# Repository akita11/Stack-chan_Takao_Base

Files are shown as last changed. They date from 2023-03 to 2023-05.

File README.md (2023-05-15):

# Stack-chan_Takao_Base

現時点で ｽﾀｯｸﾁｬﾝ を組み立てる最もシンプルな方法と思われる、[タカオさん](https://twitter.com/mongonta555)の[タカオ版（旧称：GoBottom版）](https://mongonta.booth.pm/)のための、M5Stack本体と2個のサーボモータ、給電用のUSB TypeCコネクタがついたボードです。電源スイッチもついています。まるごと一式、タカオ版のサーボ固定部分(Bracket)に収納できます。市販のUSB Type-CコネクタつきのACアダプタ等をつないで給電して使用します。以下のように、本体の後ろ側からUSB Type-Cケーブルで給電して動作させることができます。

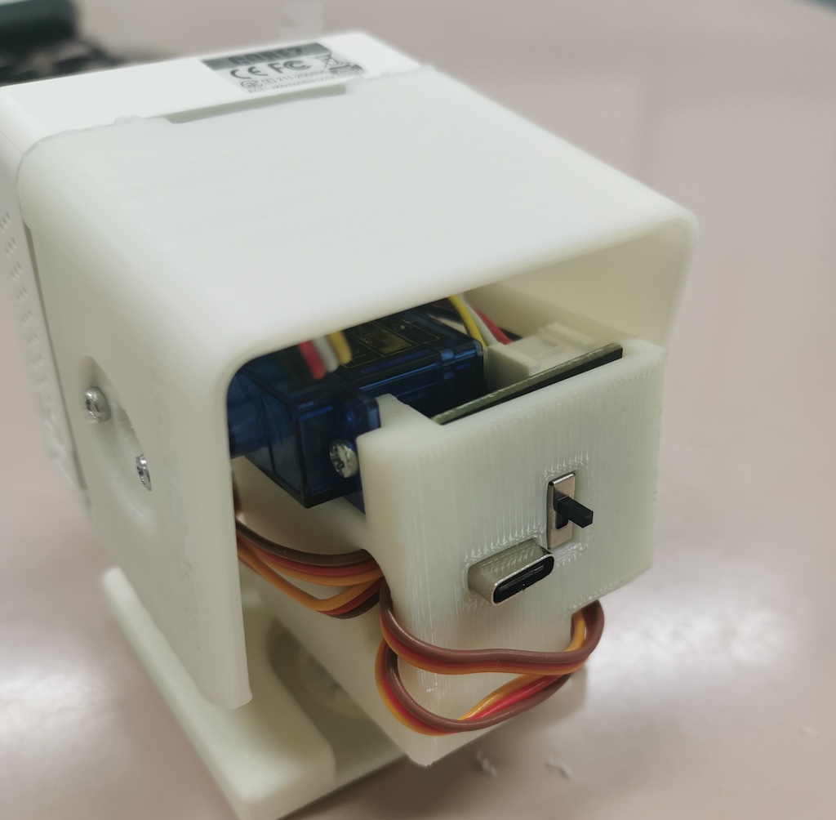
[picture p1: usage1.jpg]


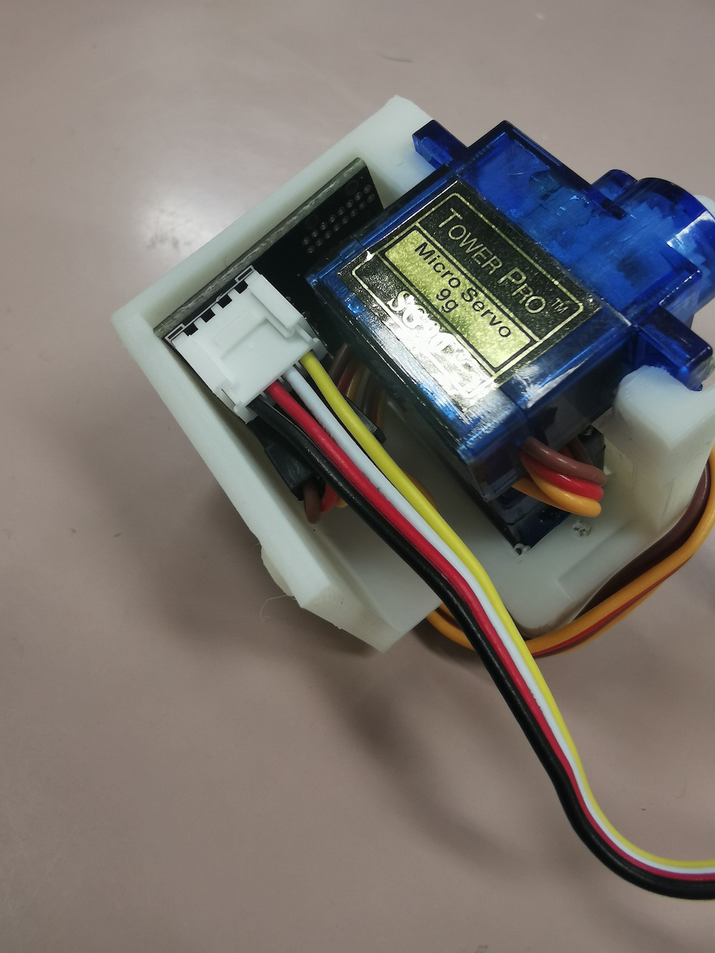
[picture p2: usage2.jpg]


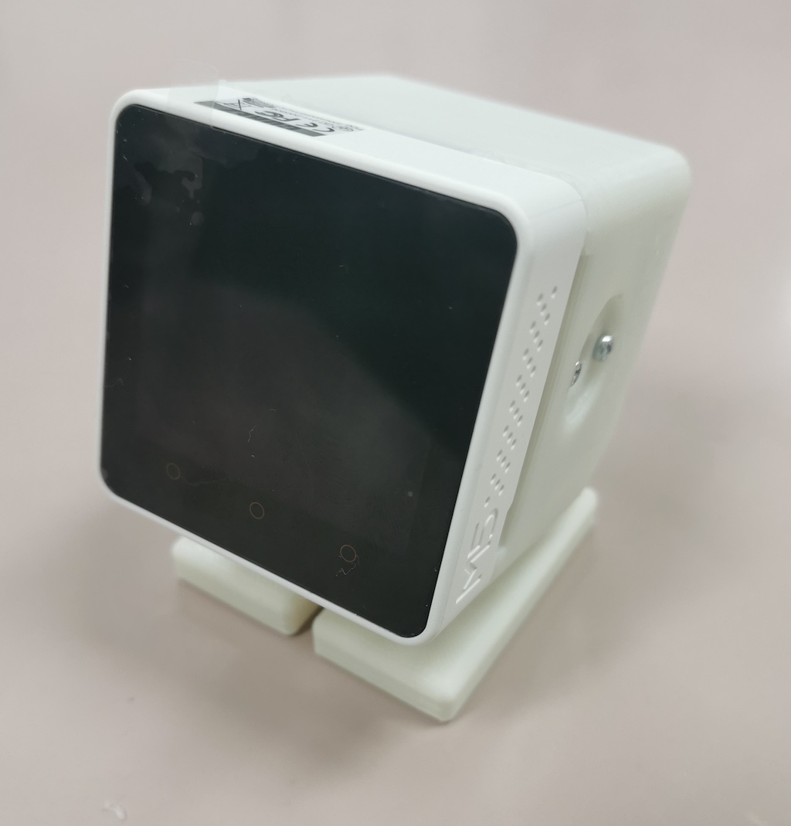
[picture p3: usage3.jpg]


## 表面実装部品版

※[完成品としてスイッチサイエンスで委託販売中](https://www.switch-science.com/products/8905)です

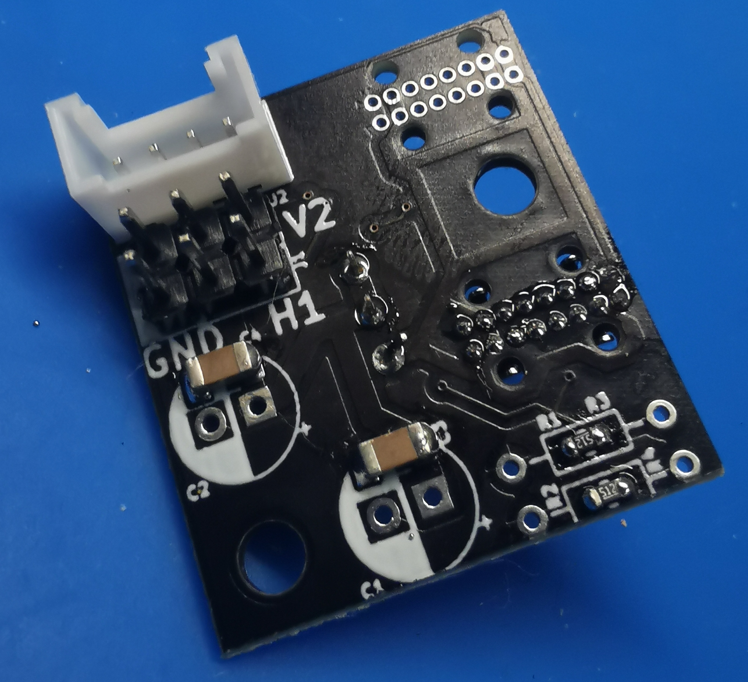
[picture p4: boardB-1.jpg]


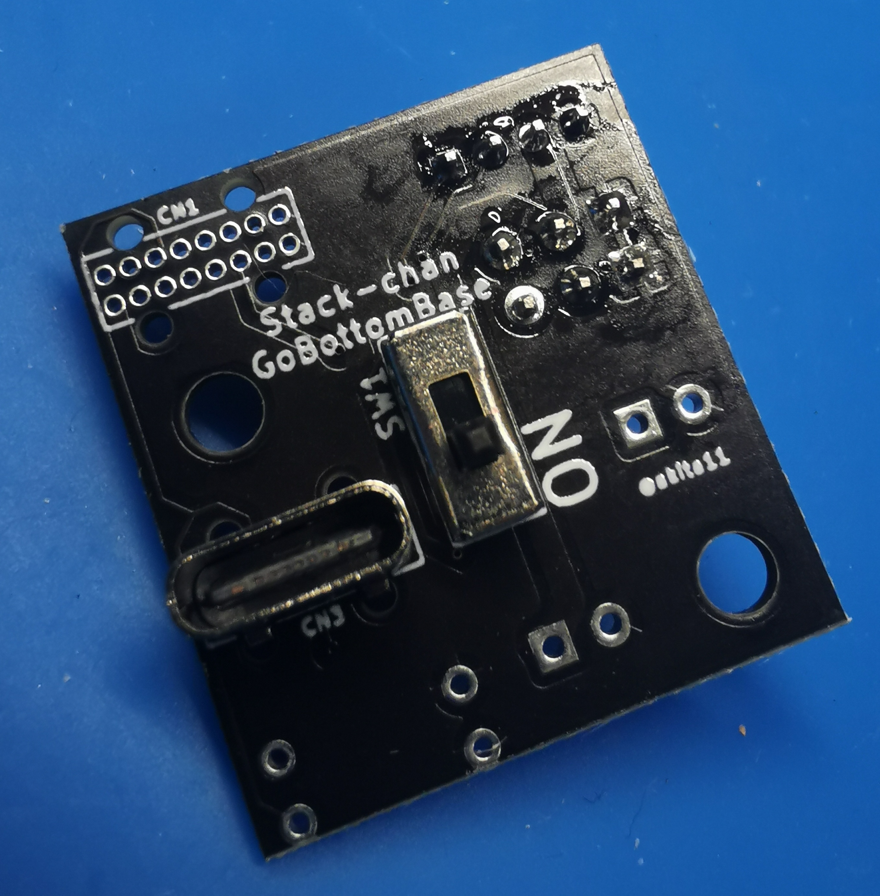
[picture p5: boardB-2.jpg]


## 挿入実装部品版

※[部品キットとしてスイッチサイエンスで委託販売中](https://www.switch-science.com/products/8906)です

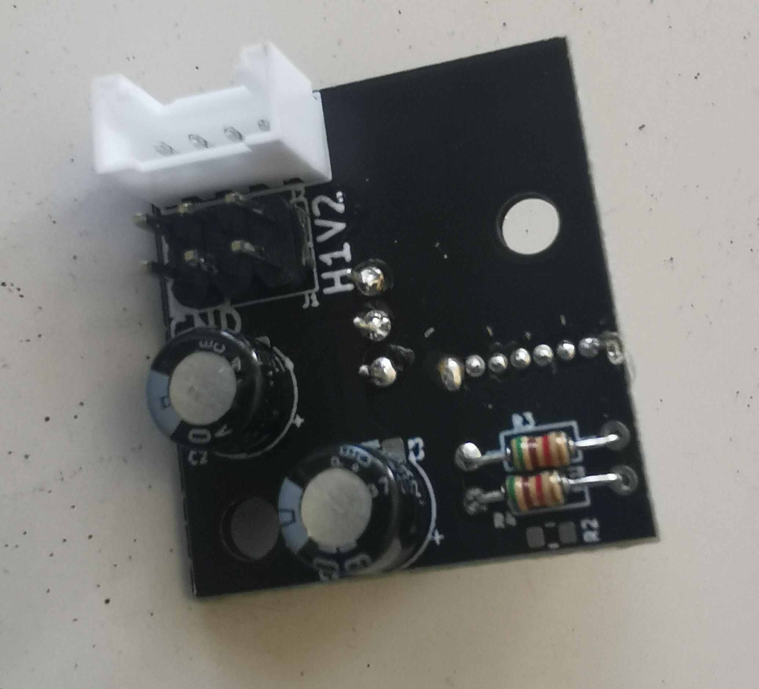
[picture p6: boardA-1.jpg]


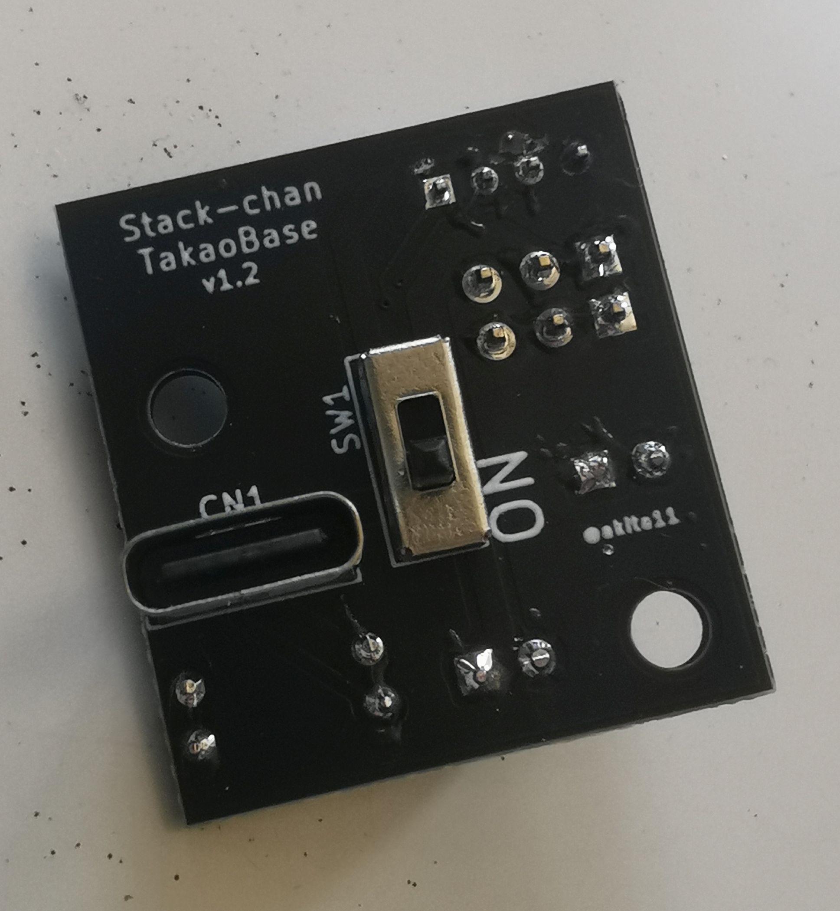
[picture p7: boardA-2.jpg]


※部品キット版では、[作り方](https://github.com/akita11/Stack-chan_Takao_Base/blob/main/Build/README.md)の手順で部品をはんだ付けしてください。

## 他に用意するもの

- M5Stack本体 (Core BasicまたはCore2がおすすめ）
- サーボモータ2個 ([FS90MG](https://www.switch-science.com/products/8041)や[M5Stack ServoKit 180deg](https://www.switch-science.com/products/6478)、[SG90](https://akizukidenshi.com/catalog/g/gM-08761/)など)
- Groveケーブル ([M5Stack用5cm](https://www.switch-science.com/products/8664)など。すでにM5StackのUNITなどで余っているものがあればそれでもOK）
- ["タカオ版（旧称：GoBottom版）"の筐体一式](https://mongonta.booth.pm/)、または[それの3Dデータ](https://github.com/meganetaaan/stack-chan/tree/dev/v1.0/case/contributed/mongonta_case_for_SG90_and_M5GoBottomBoard)を3Dプリント出力したものと必要なネジ類

## 使い方

- 筐体の組み立てなどは、[タカオさんの手順](https://raspberrypi.mongonta.com/how-to-build-easy-stackchan-m5gobottom/)を参考に行います。
- M5Stack本体と本ボードはGroveケーブルで接続します
- 2個のサーボを本ボードに接続します。ボード上の「H1」側には水平方向（足側）のサーボを、「V2」側には上下方向（筐体側）のサーボを接続します。いずれも、サーボのGND側（茶色や黒のケーブル側）を、本ボードの端側（白マークのある側）に挿し込みます。
- 本ボードを、Bracket（サーボを固定している部品）に収めます。必要に応じて両面テープやネジなどで固定してください。

## うまく動作しないときは・・・

「バッテリをはずしたCore2にこのボードとサーボを接続し、Core2側にUSBケーブルをつないでプログラムの書き込みを行う」場合に、Core2が起動しない、またはリセット・再起動を繰り返す、という現象があるようです。その場合は、いったんGroveケーブルをはずしてCore2単体でプログラムを書き込んでから、このボードのUSBコネクタ（本体背面）から電源を供給して使用してください。

## おまけ：本ボードを作りたい人は・・・

- 基板を製造します (ガーバーデータ=Stack-chan_Takao_Base_gerber.zip)
- 部品を用意します（部品リスト=Stack-chan_Takao_Base_BOM.csv) 主な部品は秋月電子で購入できます。USBコネクタのみ、[AliExpress](https://ja.aliexpress.com/item/1005004175942555.html)などから購入します（汎用品のようで、互換の製品が多数あります）

  - 挿入実装版（はんだ付けに自信のない方向け）: 抵抗とコンデンサはC1, C2, R3,R4を使います。
  - 表面実装版（はんだ付けに自信のある方向け）: 抵抗とコンデンサはC3, C4, R1,R2を使います。

## Author

Junichi Akita (akita@ifdl.jp, @akita11)

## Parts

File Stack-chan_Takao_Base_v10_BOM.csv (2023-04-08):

Designator | Footprint | Quantity | Value | LCSC Part #
C1, C2 | CP_Radial_D6.3mm_P2.50mm | 2 | 100u | https://akizukidenshi.com/catalog/g/gP-05002/ |  | ※組み立てキット用
C3, C4 | C_1206_3216Metric | 2 | 100u | C312983 |  | ※量産SMD用
CN1, CN3 | USB-C_16p_V_TH | 2 | CON_USB-C-16p | C2848615
CN2 | CON_GROVE_V | 1 | CON_GROVE | C2845462
J1, J2 | PinHeader_1x03_P2.54mm_Vertical | 2 | Conn_01x03 | C429954 | https://akizukidenshi.com/catalog/g/gC-03949/
R1, R2 | R_0603_1608Metric | 2 | 5.1k | C23186 |  | ※量産SMD用
R3, R4 | R_Axial_DIN0204_L3.6mm_D1.6mm_P7.62mm_Horizontal | 2 | 5.1k |  | https://akizukidenshi.com/catalog/g/gR-16512/ | ※組み立てキット用
SW1 | SW_SPDT_9x4mm_W2.5mm | 1 | SW_SPDT |  | https://akizukidenshi.com/catalog/g/gP-12723/

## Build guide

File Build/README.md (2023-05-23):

# Stack-chan_Takao_Base（部品キット版）の作り方





挿入実装部品版（部品キット版）の組み立て手順です。

## 用意するもの（部品一式）

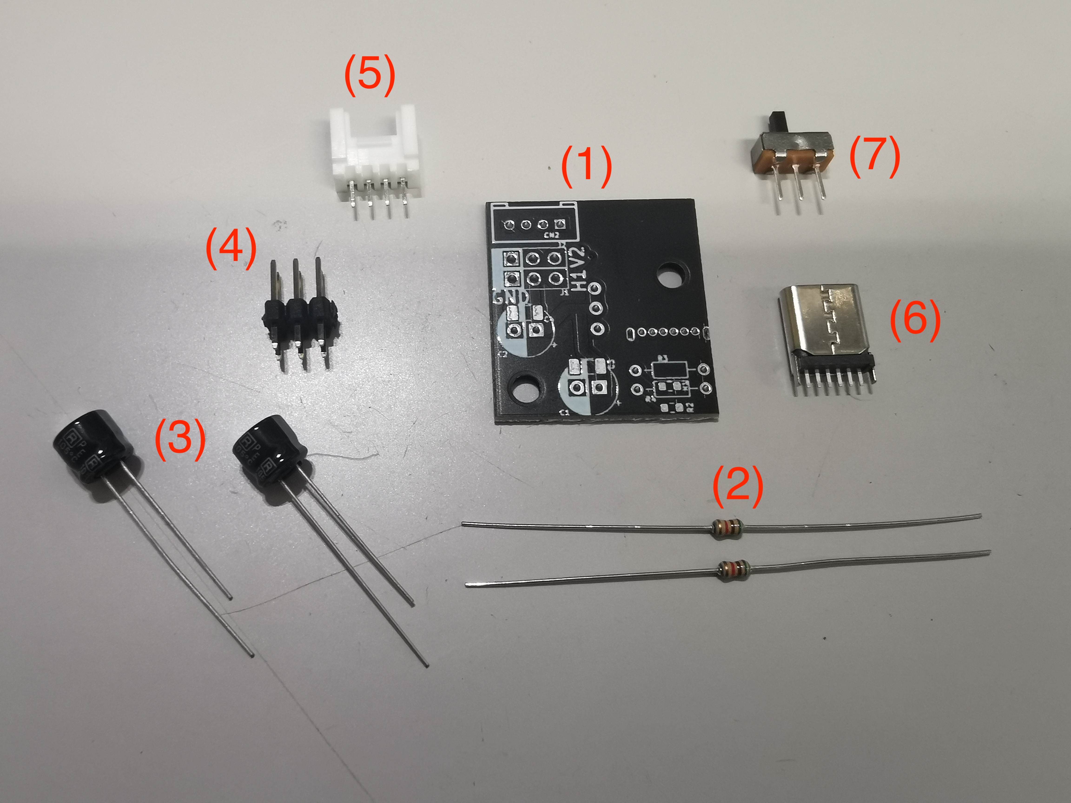
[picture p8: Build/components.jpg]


- (1)基板：1個
- (2)抵抗(5.1kΩ)：2本
- (3)コンデンサ(100uF)：2個
- (4)ピンヘッダ(3p)：2個（※3p×2列のものが1個の場合もあります）
- (5)Groveコネクタ：1個
- (6)USB Type-Cコネクタ：1個
- (7)電源スイッチ：1個

## 抵抗のとりつけ

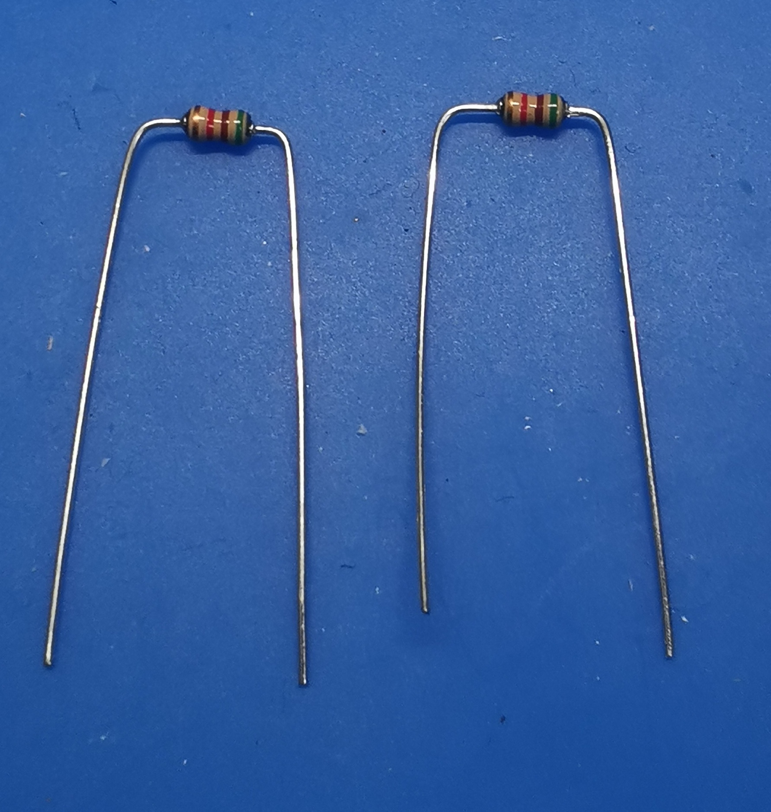
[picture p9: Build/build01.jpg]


(2)抵抗の足を、これぐらいの間隔で90度に折り曲げます。



それを(1)基板のこの位置に、奥まで差し込みます。

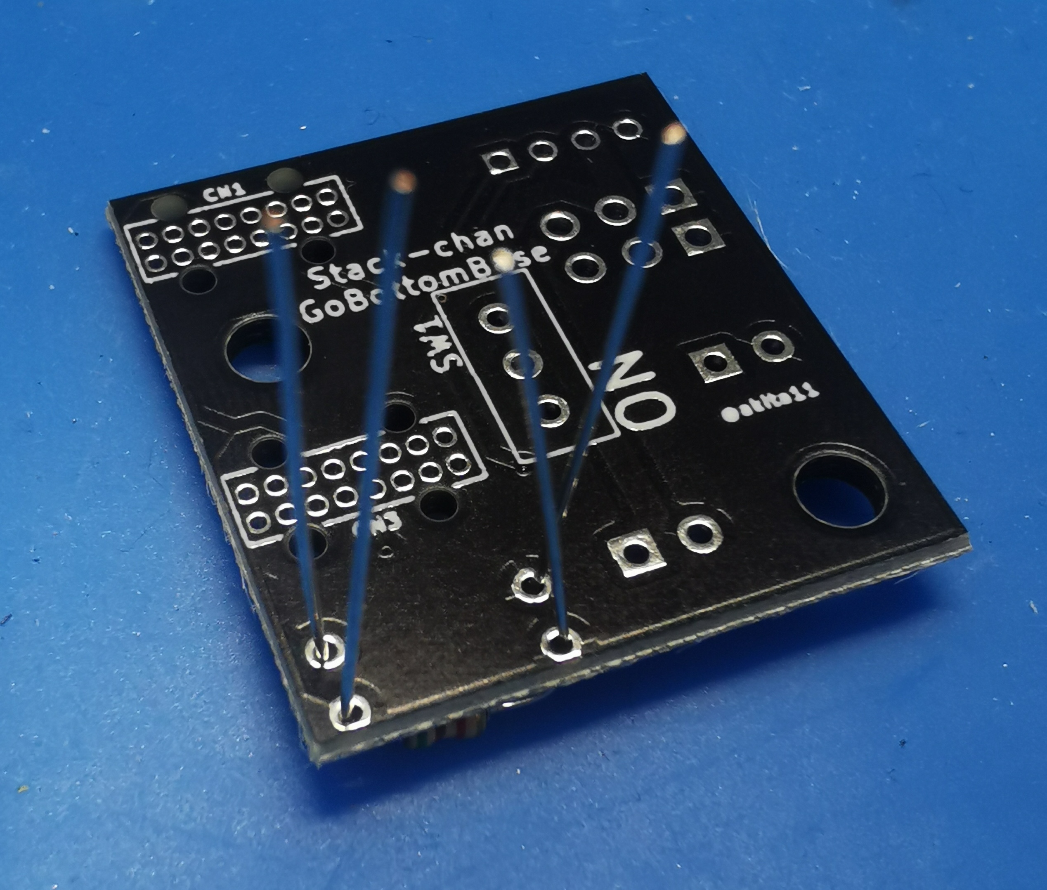
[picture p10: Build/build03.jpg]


裏から見るとこんな感じ。

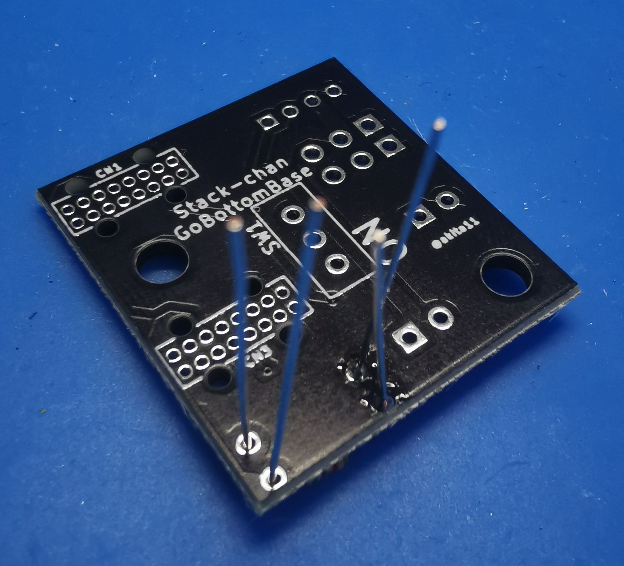
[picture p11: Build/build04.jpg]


それぞれの(2)抵抗の片側をはんだ付けします

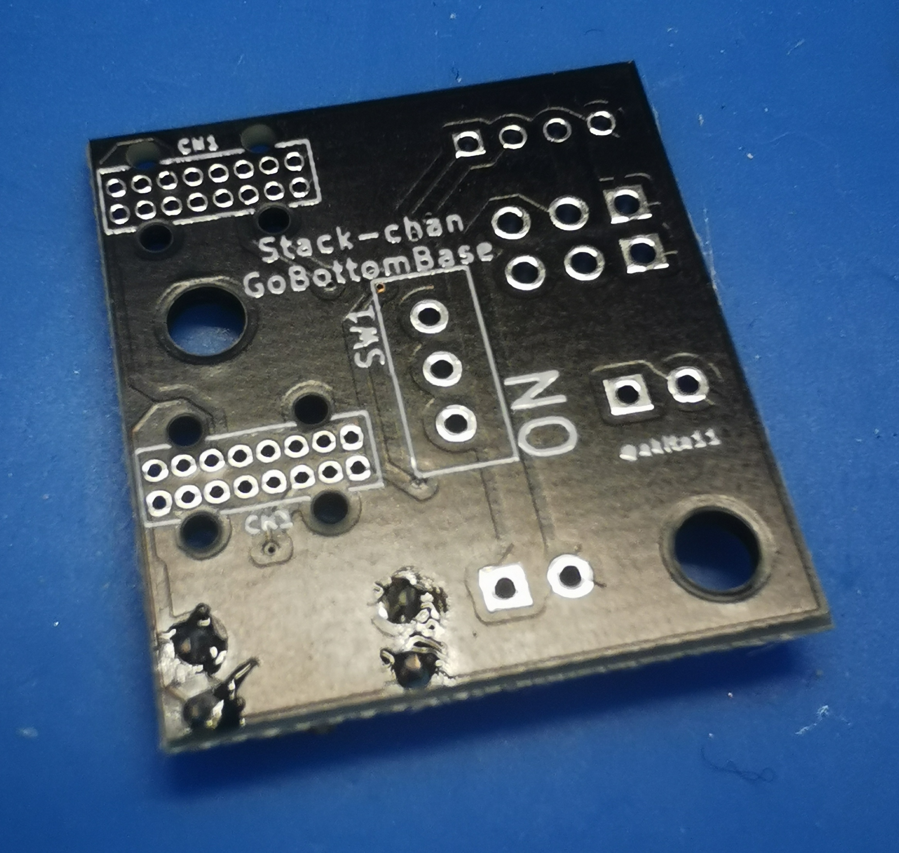
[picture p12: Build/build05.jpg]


表面で(2)抵抗が(1)基板から浮いていないことを確認し（浮いていたら、はんだを溶かしながら押し込む。多少は浮いていてもOK）、残りの足をはんだ付け。

## コンデンサのとりつけ

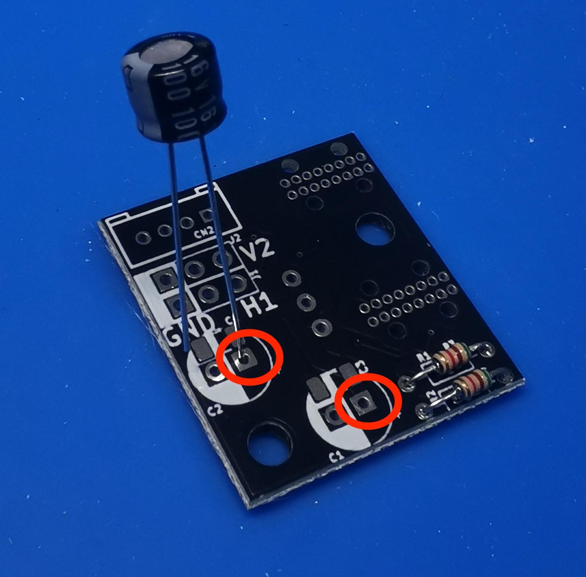
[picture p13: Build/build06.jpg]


(3)コンデンサの2本の足のうち、長い方を、この赤丸の側（銀色部が四角い方）にさしこみます。

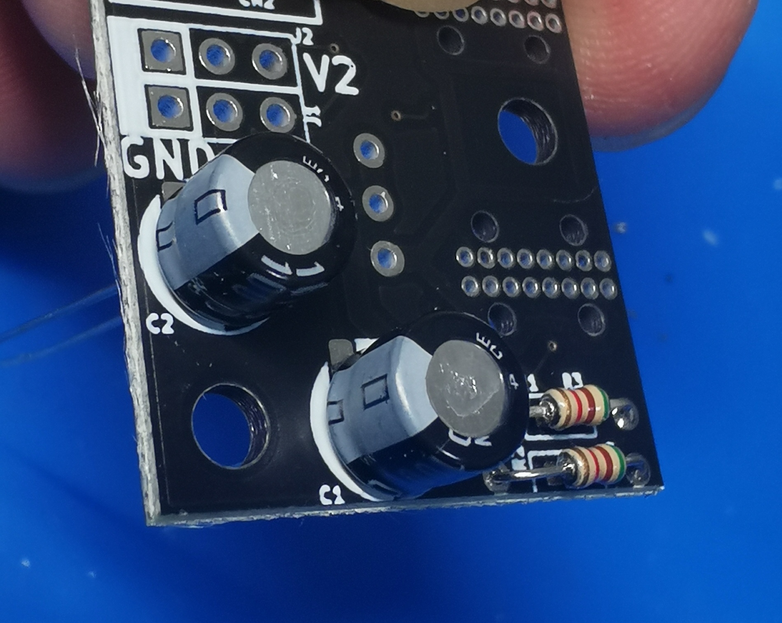
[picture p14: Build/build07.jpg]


奥までさしこみます。

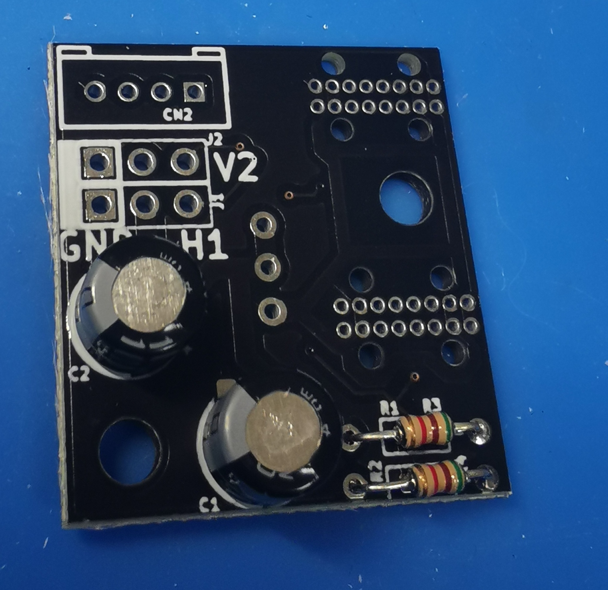
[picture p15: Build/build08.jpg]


裏面で(3)コンデンサの足をはんだ付けします。(2)抵抗のときと同じように、まず片側をはんだ付けし、(1)基板から浮いていないのを確認してからもう一方をはんだ付けするとよいです。

## ピンヘッダのとりつけ

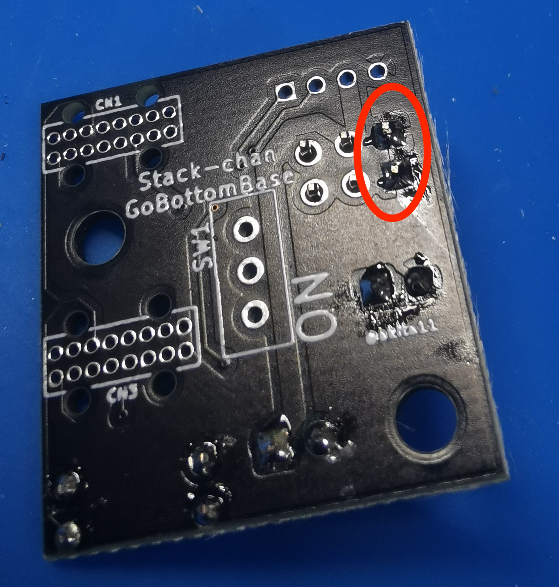
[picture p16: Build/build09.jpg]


(4)ピンヘッダの短い側の足を(1)基板に差し込み、浮かないようにおさえながら、1箇所をはんだ付けします。

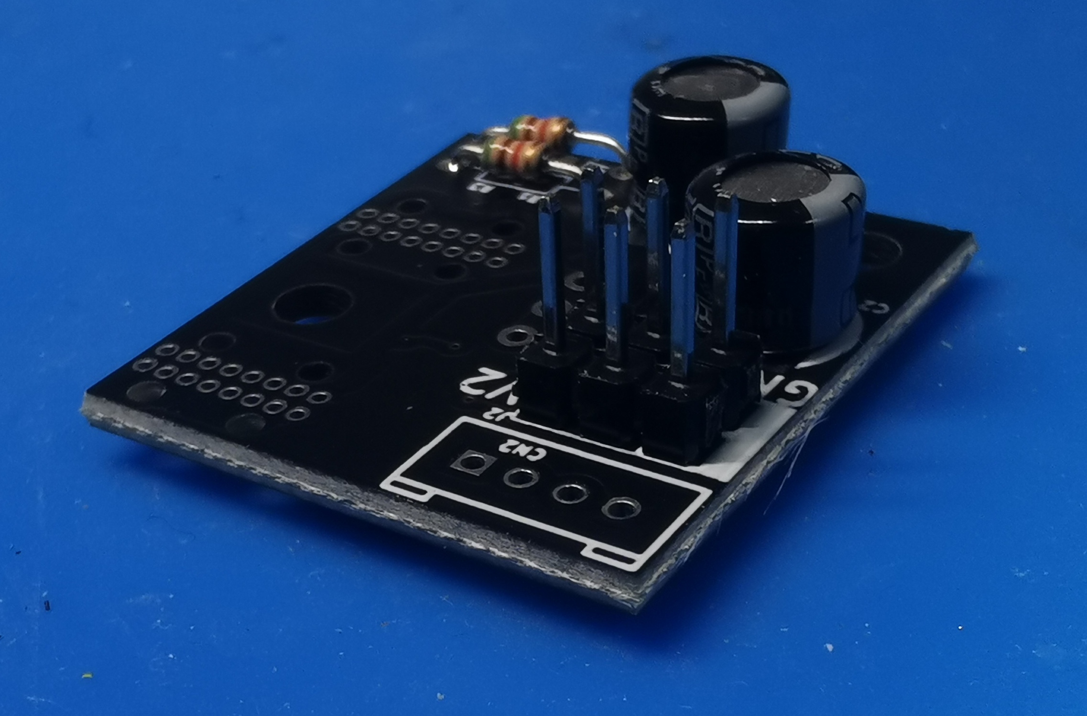
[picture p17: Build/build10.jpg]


浮いていないことを確認。浮いていたら、押さえながらはんだをとかして押し付けます。

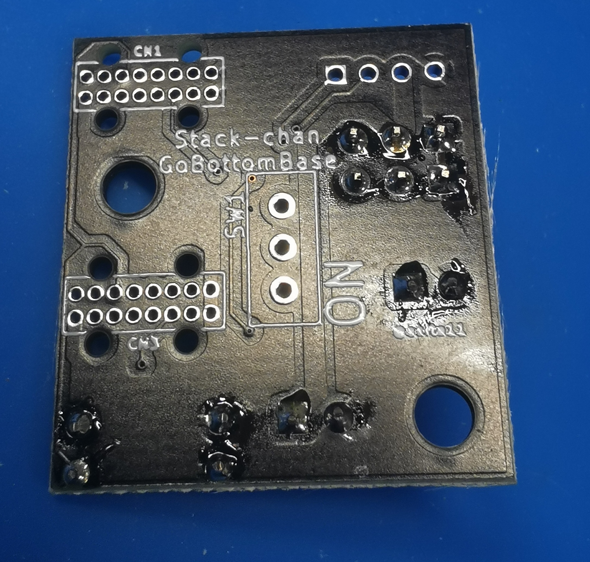
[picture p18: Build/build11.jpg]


浮いていないことを確認したら、残りの足をはんだ付けします。

## Groveコネクタのとりつけ

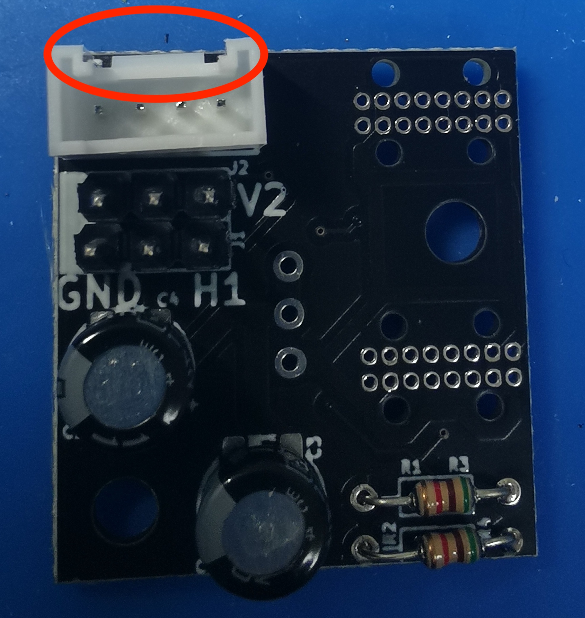
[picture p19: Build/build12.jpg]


(5)Groveコネクタを、赤丸の切り欠きの向きがこの通りになるようにさしこみ、浮かないように注意しながらはんだ付けします。

## USBコネクタのとりつけ

*※ここから先は、(1)基板の反対側の面に部品をとりつけます。(1)基板の部品を取り付ける位置に、白い四角い枠があるのを確認して部品をとりつけてください。くれぐれも逆側にとりつけないように注意！*

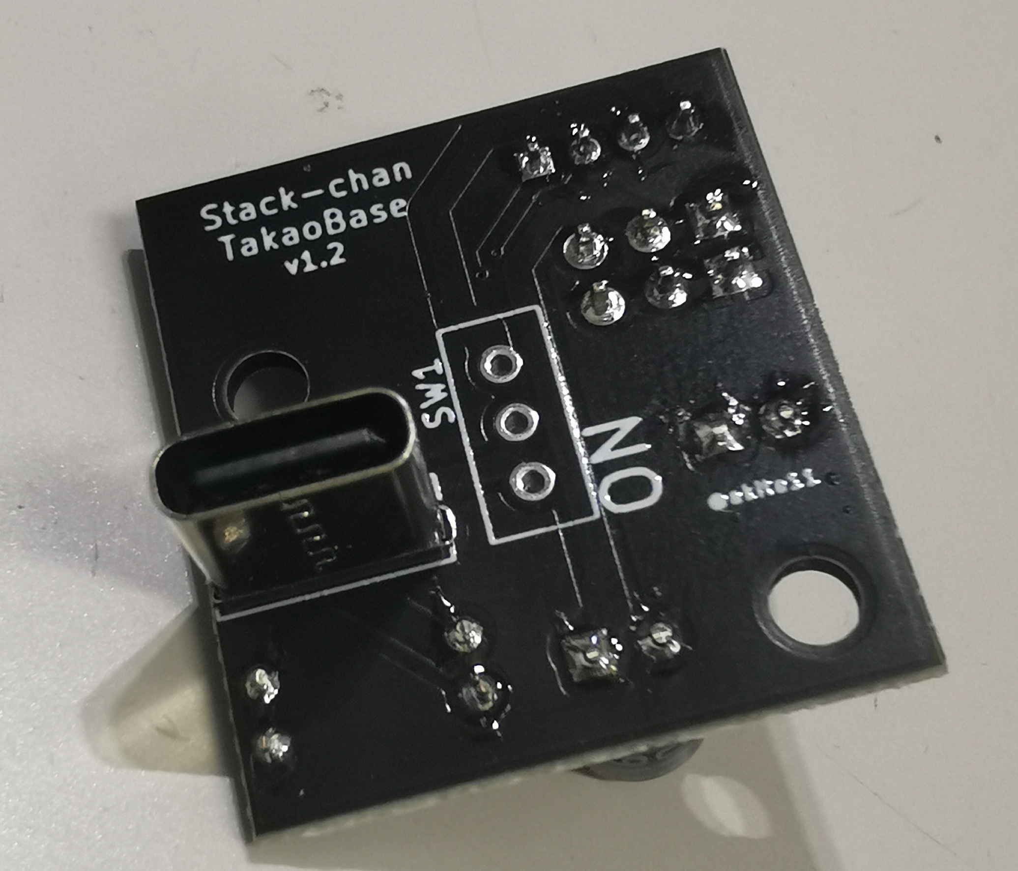
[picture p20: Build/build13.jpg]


(6)USBコネクタをさしこみます。

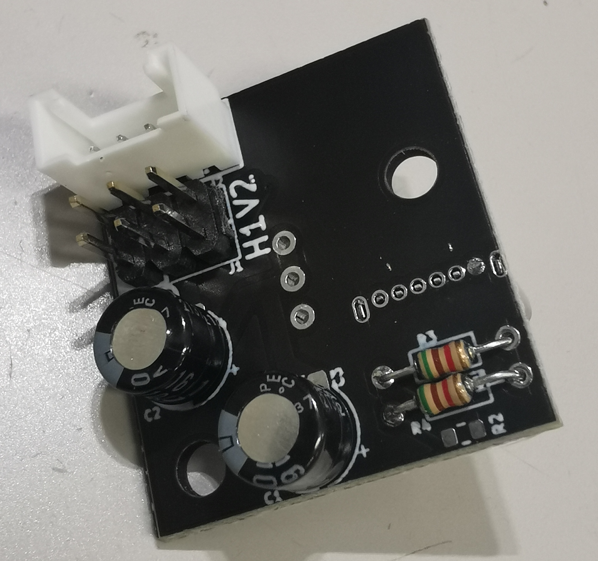
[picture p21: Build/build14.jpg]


浮かないように注意ながら、まず1箇所だけはんだ付けします。はんだ付けする箇所がとても小さいですが、はんだがとなりとショートしないようにはんだの量に注意します。もしはんだが多すぎてショートしてしまったら、あわてずにはんだごてでちょんちょんとすれば、はんだが取り除けます。
*端子の間隔が狭く、ショートしやすいので、十分に注意しましょう*

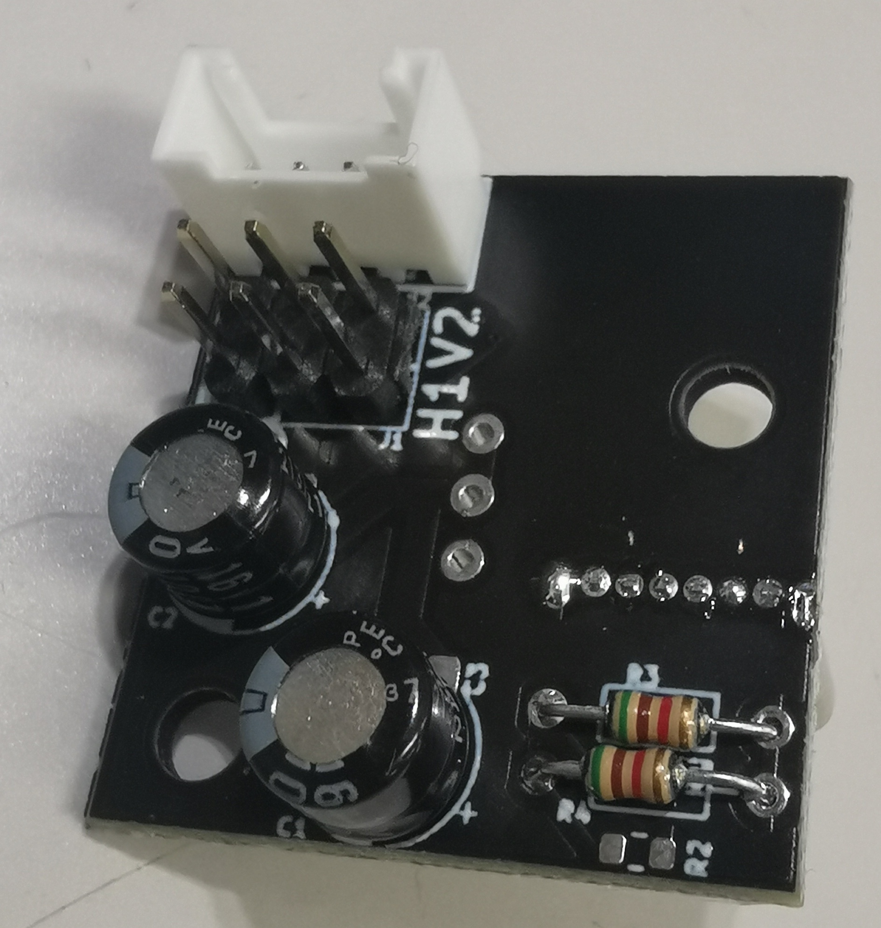
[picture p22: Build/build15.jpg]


浮いていないのを確認したら、残りをはんだ付けします。

## 電源スイッチのとりつけ

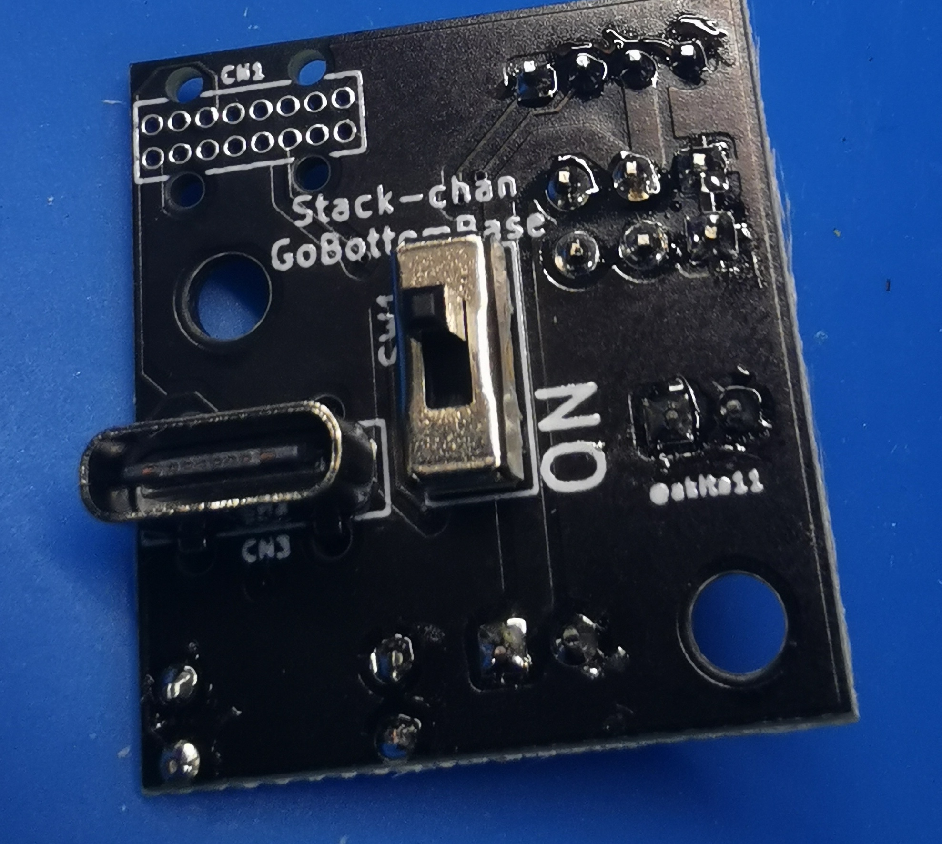
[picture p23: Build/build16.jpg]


(7)電源スイッチをさしこみます。

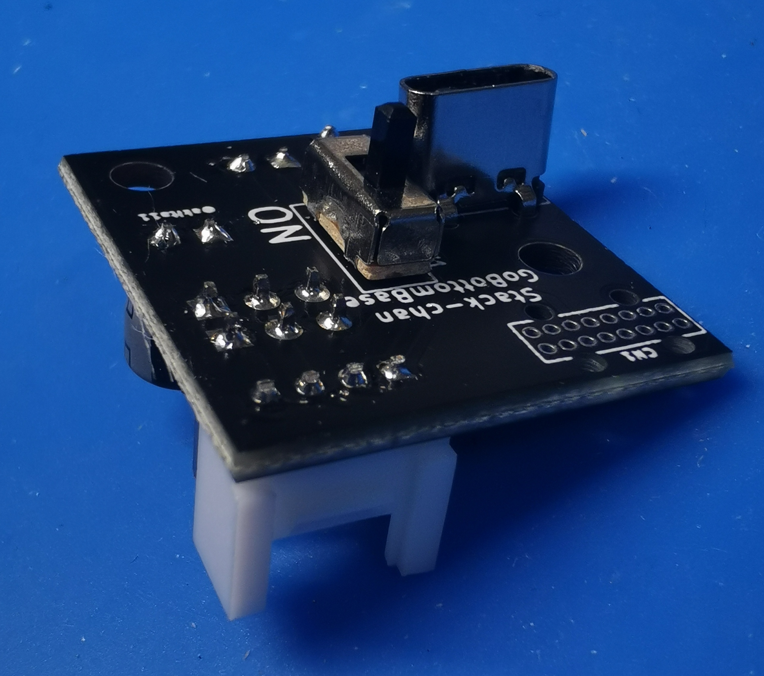
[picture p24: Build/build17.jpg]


これまでと同じように、浮かないように注意しながら、まず1箇所、浮いていないのを確認してから、残りをはんだ付けします。





完成！

## Author

Junichi Akita (akita@ifdl.jp, @akita11)

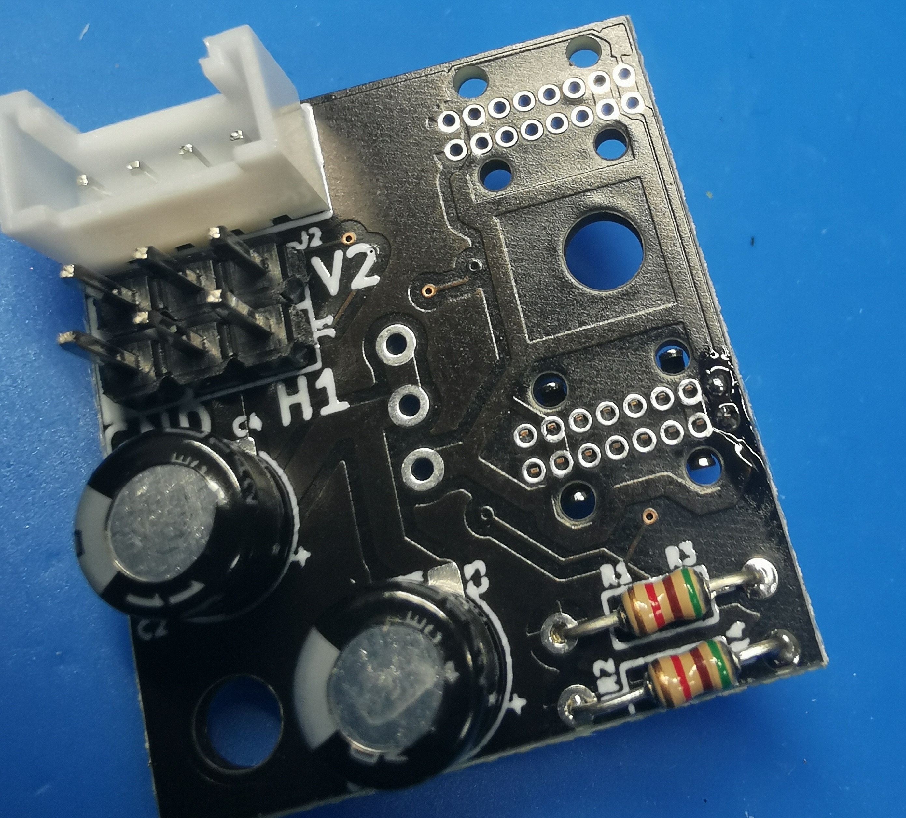
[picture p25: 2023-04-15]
Build/build14_1st.jpg

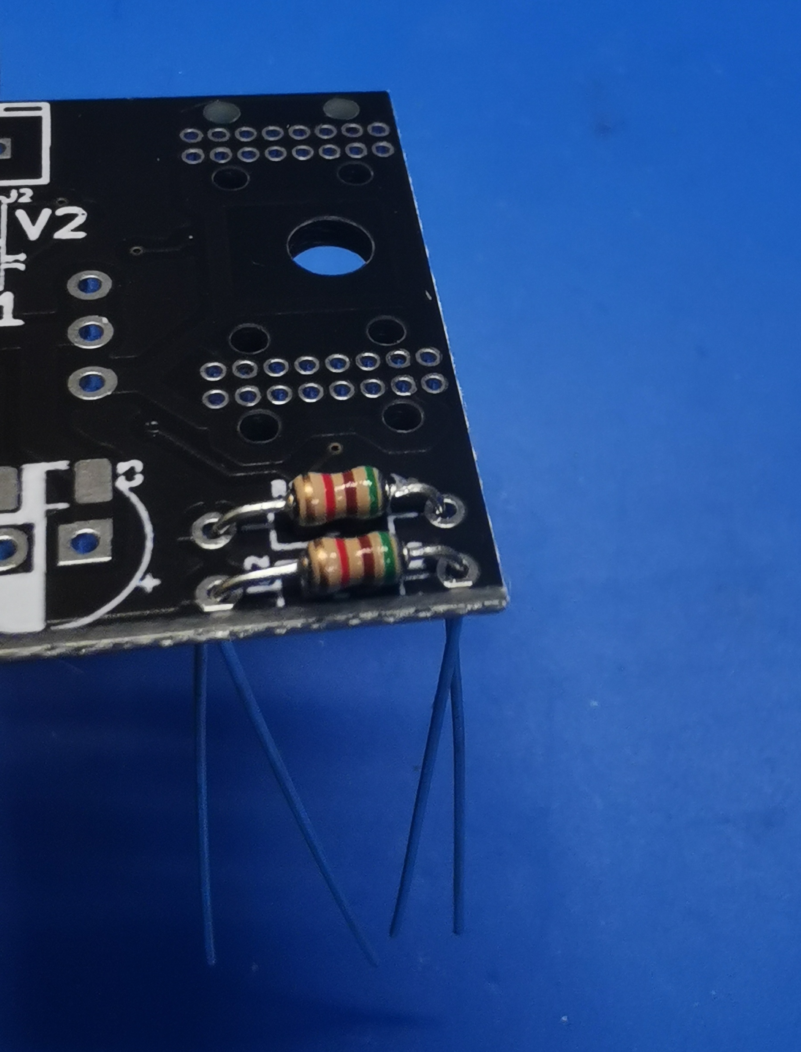
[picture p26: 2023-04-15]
Build/build02.jpg

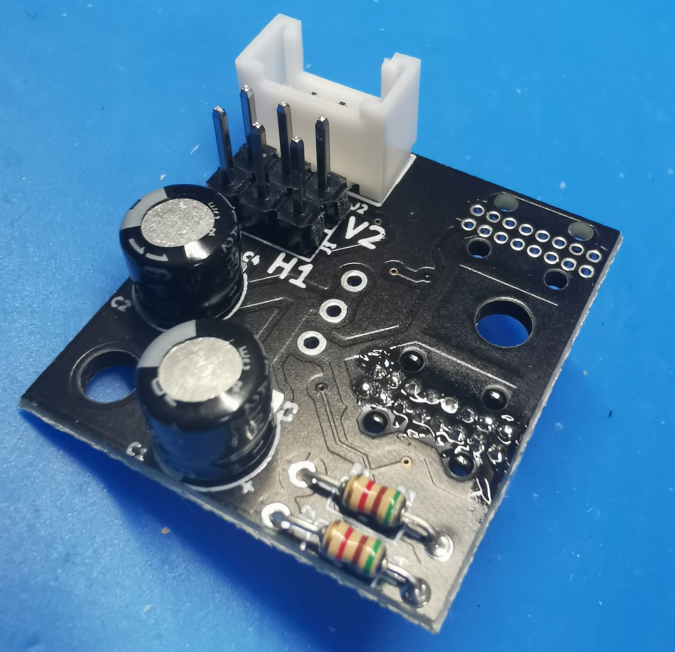
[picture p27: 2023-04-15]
Build/build15_1st.jpg

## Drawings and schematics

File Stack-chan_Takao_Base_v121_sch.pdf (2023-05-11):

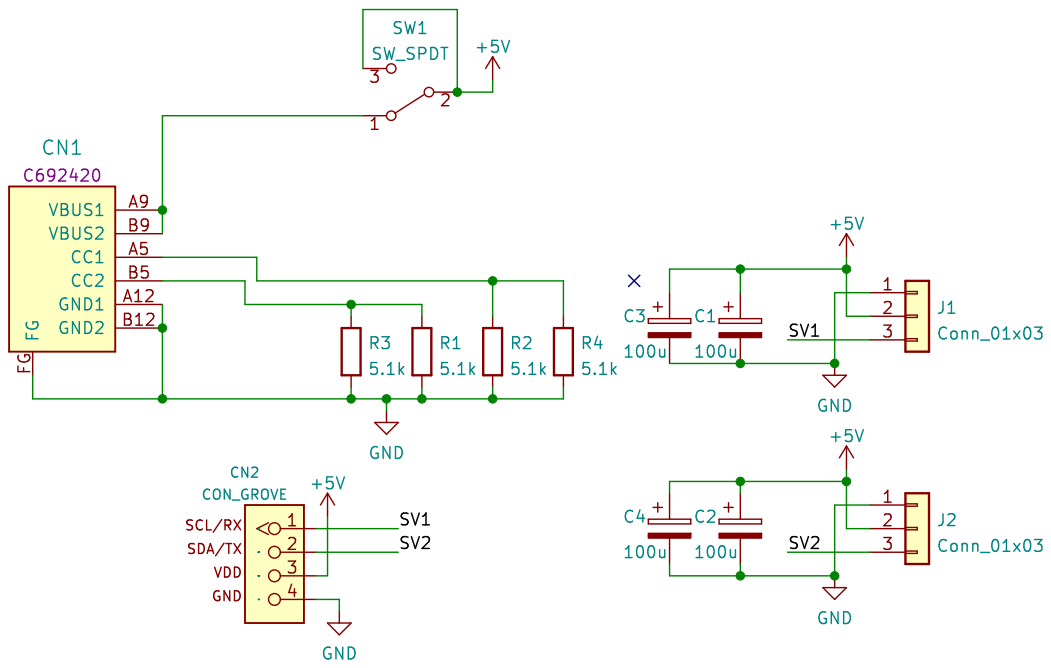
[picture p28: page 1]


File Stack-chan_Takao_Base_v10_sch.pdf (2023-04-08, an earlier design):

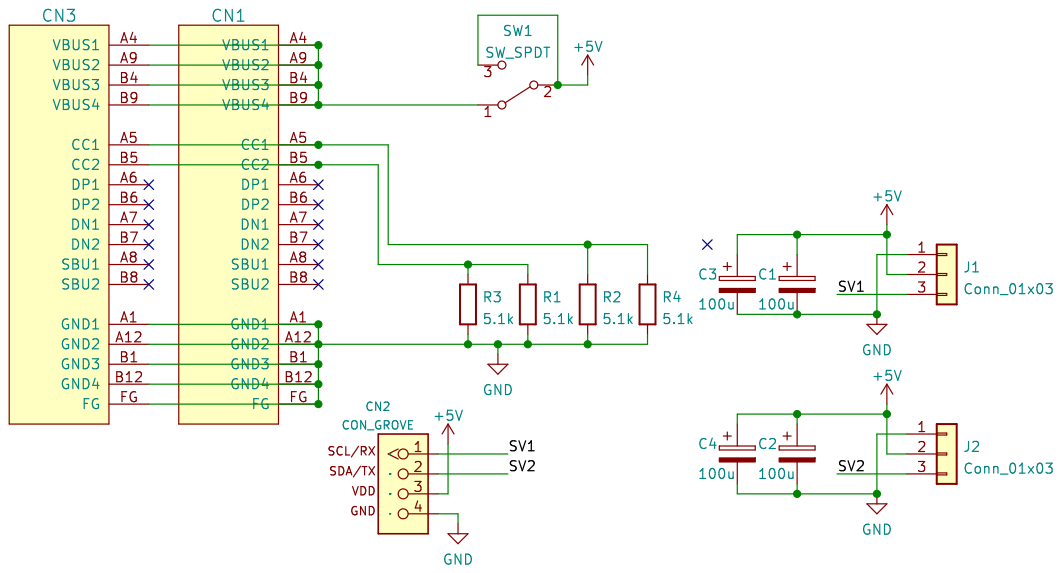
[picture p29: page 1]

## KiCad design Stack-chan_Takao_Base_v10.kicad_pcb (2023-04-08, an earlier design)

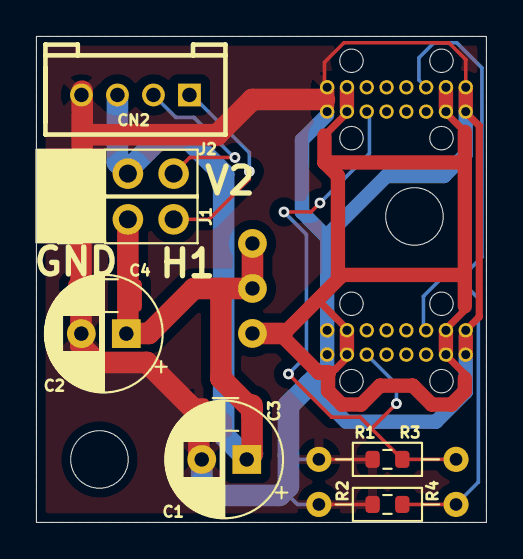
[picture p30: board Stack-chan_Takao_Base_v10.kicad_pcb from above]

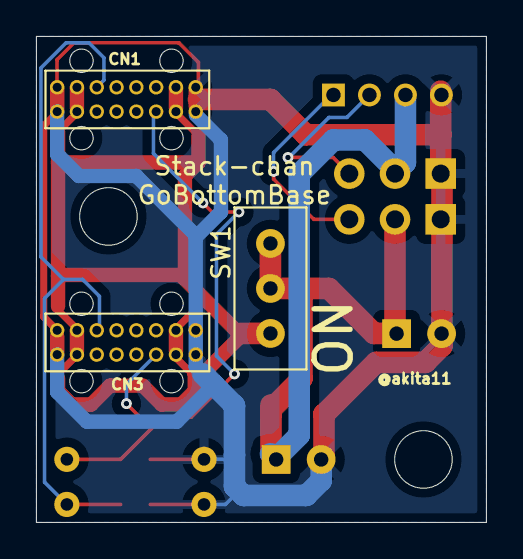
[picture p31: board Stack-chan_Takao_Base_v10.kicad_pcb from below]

Board: 2 copper layers, 25.0 x 27.0 mm, 14 parts (3 on the bottom side), 7 nets.

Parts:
C1, C2: 100u; CP_Radial_D6.3mm_P2.50mm
C3, C4: 100u; C_1206_3216Metric
CN1, CN3: CON_USB-C-16p; USB-C_16p_V_TH
CN2: CON_GROVE; CON_GROVE_V
J1, J2: Conn_01x03; PinHeader_1x03_P2.54mm_Vertical
R1, R2: 5.1k; R_0603_1608Metric
R3, R4: 5.1k; R_Axial_DIN0204_L3.6mm_D1.6mm_P7.62mm_Horizontal
SW1: SW_SPDT; SW_SPDT_9x4mm_W2.5mm

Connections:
+5V: C1.1, C2.1, C3.1, C4.1, CN2.3, J1.2, J2.2, SW1.2 (B), SW1.3 (C)
/SV1: CN2.1, J1.3
/SV2: CN2.2, J2.3
GND: C1.2, C2.2, C3.2, C4.2, CN1.A1 (GND1), CN1.A12 (GND2), CN1.B1 (GND3), CN1.B12 (GND4), CN2.4, CN3.A1 (GND1), CN3.A12 (GND2), CN3.B1 (GND3), CN3.B12 (GND4), J1.1, J2.1, R1.2, R2.2, R3.2, R4.2
unnamed: CN1.A4 (VBUS1), CN1.A9 (VBUS2), CN1.B4 (VBUS3), CN1.B9 (VBUS4), CN3.A4 (VBUS1), CN3.A9 (VBUS2), CN3.B4 (VBUS3), CN3.B9 (VBUS4), SW1.1 (A)
unnamed: CN1.A5 (CC1), CN3.A5 (CC1), R2.1, R4.1
unnamed: CN1.B5 (CC2), CN3.B5 (CC2), R1.1, R3.1

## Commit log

2023-04-03 add servo info
2023-04-08 for v1
    [Stack-chan_GoBottomBase.kicad_pcb, Stack-chan_GoBottomBase.kicad_sch, Stack-chan_GoBottomBase_BOM.csv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]
2023-04-15 add photo and Build instruction
    [Stack-chan_Takao_Base_BOM.csv]
2023-04-15 update README, powering
2023-05-11 update for v12/v121
    [Stack-chan_Takao_Base_v10.kicad_pcb, Stack-chan_Takao_Base_v10.kicad_sch, Stack-chan_Takao_Base_v10_BOM.csv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]
